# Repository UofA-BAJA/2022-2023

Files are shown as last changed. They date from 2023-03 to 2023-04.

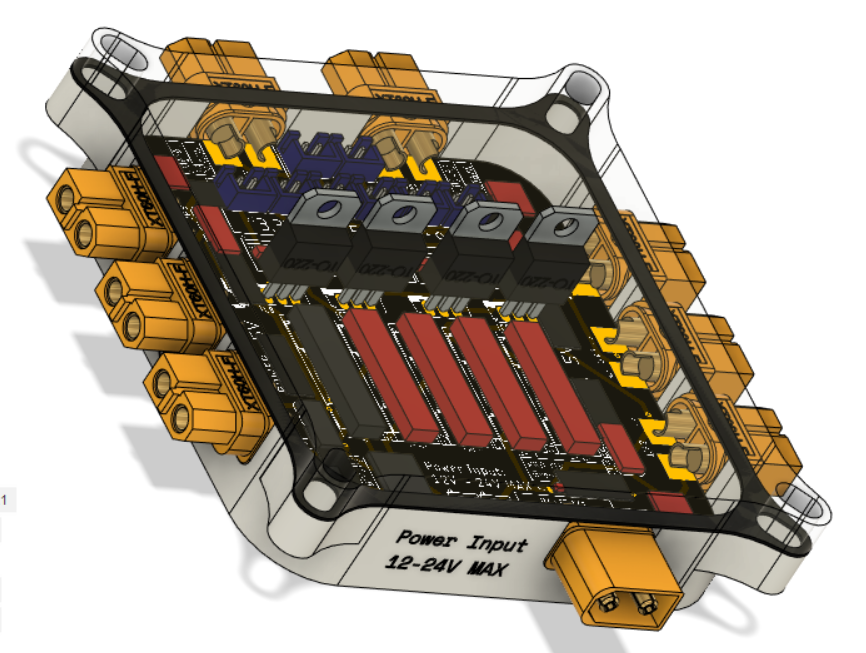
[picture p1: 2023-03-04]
res/Eagle Boards/Battery Board V1/Photos/battery_board_assembly_angle.png

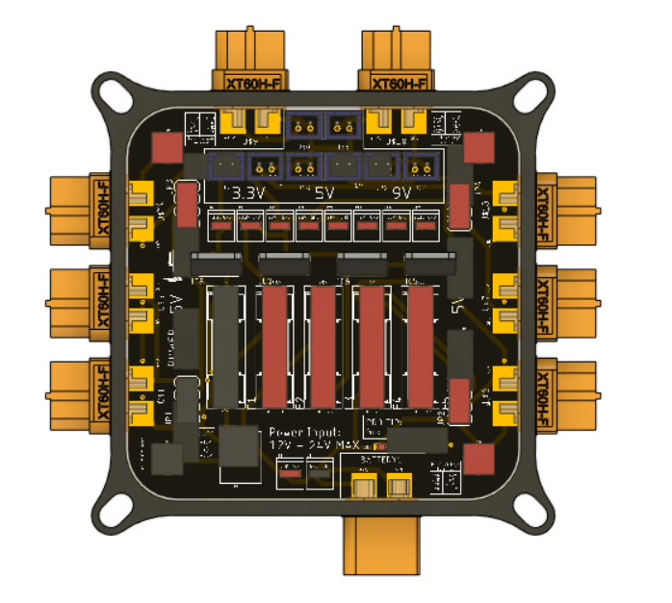
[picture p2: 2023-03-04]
res/Eagle Boards/Battery Board V1/Photos/battery_board_assembly_top.png

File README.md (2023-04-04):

# Electrical Team 2022-2023
This is the codebase for the University of Arizona BAJA Electrical Team, year 2022/2023.

[Google Drive Link](https://drive.google.com/drive/folders/1pqr16L63S9_5N_NZjZeFR-gvrg_NTns5?usp=sharing)

**This years officers and members include:**
Alex Romero (Electrical Lead),
Michael Byerly (Father),
Oliver Sjostrom,
Alyssa Pomerleau,
Henry Overbeck,
Liam Neu,
Muthu Krishnappan,
Man Doan,
Aeden Grandinetti,
Dorian Shay,
Aliah Haigh,
Juliana Levy
...

**Languages include:**
Python (Ground Station Systems),
C++ (Telemetry System),

Pull Requests into the Main Branch can be approved by Alex or Michael.
We also have a Codigna review bot that will automatically grade our code and offer suggestions in order to improve performance or legibility.

If you have any questions regarding any pieces of software or their functionality, please reach out to the officers.

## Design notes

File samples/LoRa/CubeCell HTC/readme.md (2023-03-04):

the link to the github for the HTC boards is [here](https://github.com/HelTecAutomation/CubeCell-Arduino)

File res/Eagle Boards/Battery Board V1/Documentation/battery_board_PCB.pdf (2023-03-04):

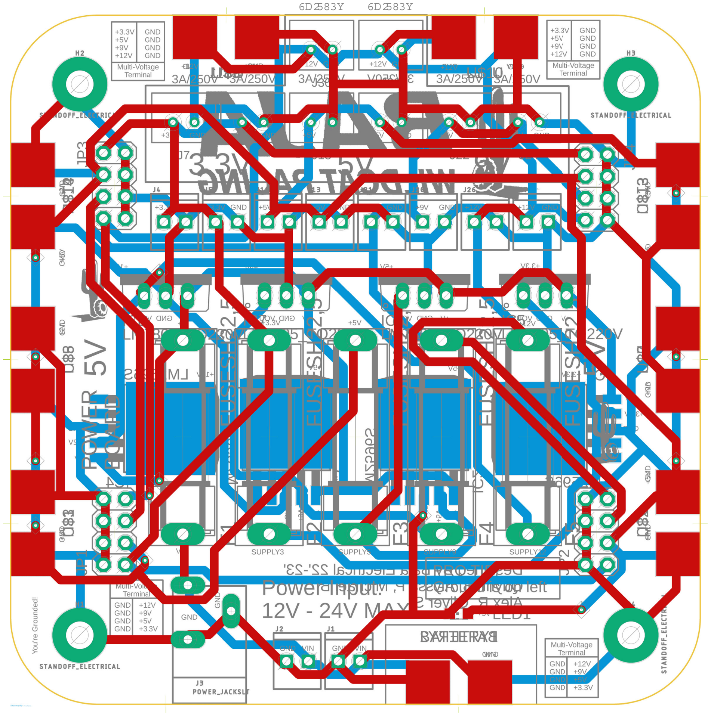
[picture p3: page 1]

3A/250V 3A/250V

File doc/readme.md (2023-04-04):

this folder is for documenation

To Get Setup
1. Install [Python](https://www.python.org/downloads/) if not installed
2. Install [VSCode](https://code.visualstudio.com/) if not installed
3. Install [Git](https://git-scm.com/download/win) and [Github Desktop](https://desktop.github.com/)
4. Open Git Repository in VSCode from Github Desktop and sign into github on VSCode
5. In terminal, execute the command "pip install PyQt5"
6. In terminal, execute the command "pip install pyqtgraph"
7. Go to src/Sensor Dashboard/\_\_main\_\_.py and hit run on VSCode

You are all setup!

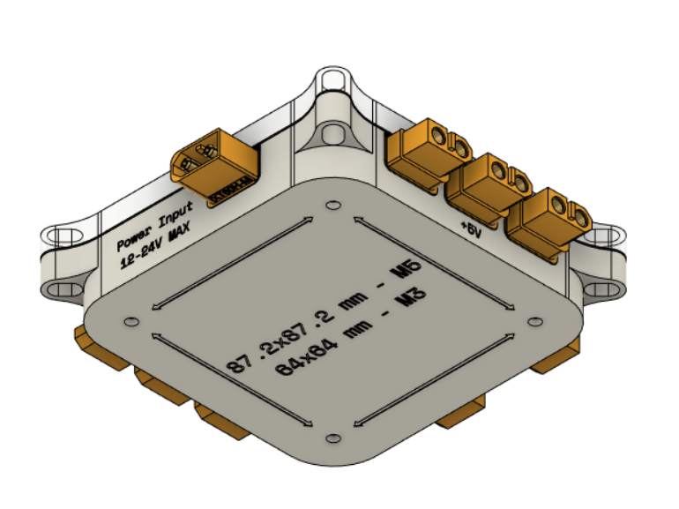
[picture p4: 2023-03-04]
res/Eagle Boards/Battery Board V1/Photos/Screenshot 2022-10-07 212603.png

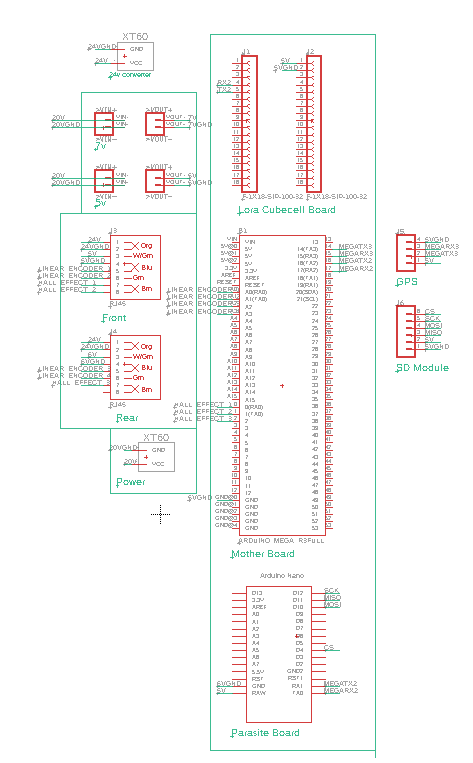
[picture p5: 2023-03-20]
res/Eagle Boards/image.png

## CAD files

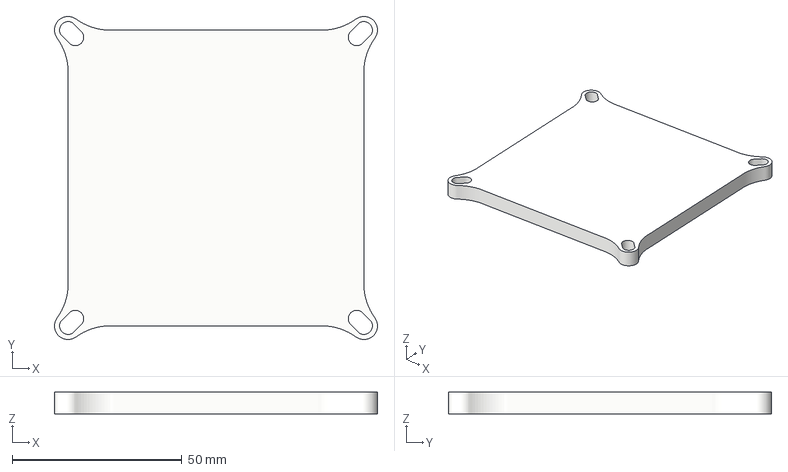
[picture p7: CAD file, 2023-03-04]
res/Eagle Boards/Battery Board V1/3D Files/Battery_Board_Lid.3mf
95.2 x 95.2 x 6.35 mm

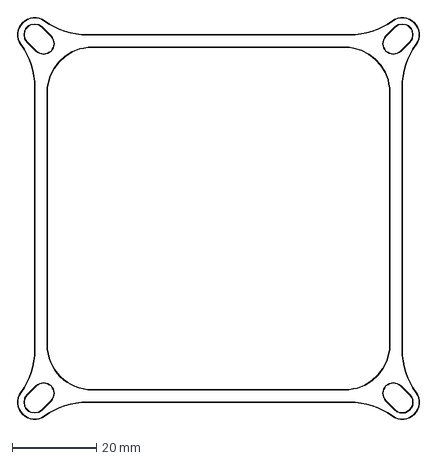
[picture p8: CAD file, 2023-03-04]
res/Eagle Boards/Battery Board V1/3D Files/Laser Cutter Files/battery_board_lid.dxf
96.0 x 96.0 mm

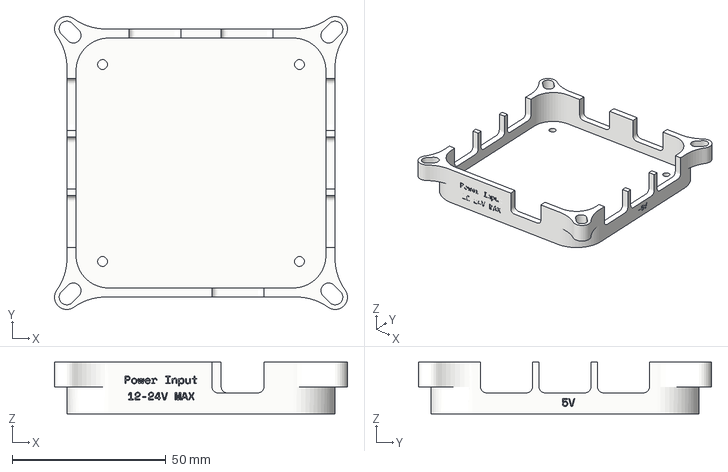
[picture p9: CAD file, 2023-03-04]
res/Eagle Boards/Battery Board V1/3D Files/Battery_Board_Case.3mf
95.2 x 95.2 x 16.8 mm

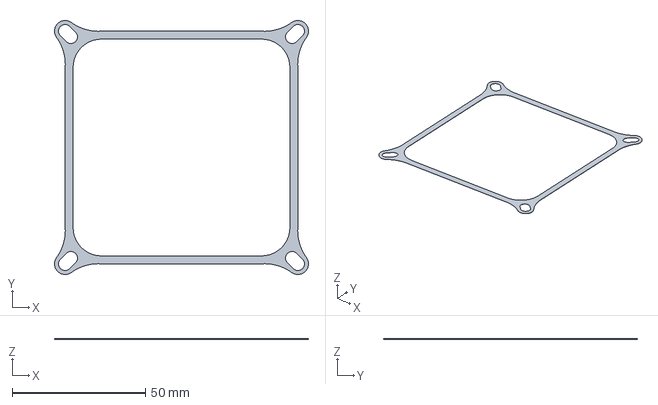
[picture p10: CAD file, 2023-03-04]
res/Eagle Boards/Battery Board V1/3D Files/Battery_Board_Seal.3mf
95.2 x 95.2 x 0.5 mm

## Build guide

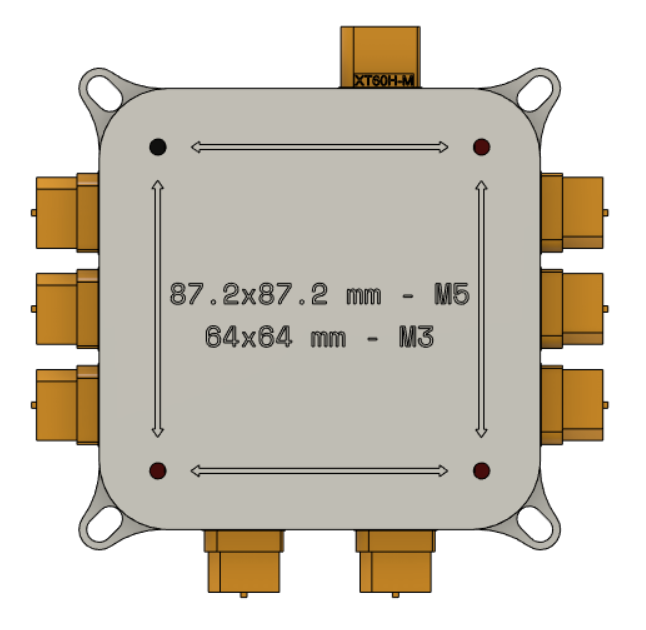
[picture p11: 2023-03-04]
res/Eagle Boards/Battery Board V1/Photos/battery_board_assembly_bottom.png

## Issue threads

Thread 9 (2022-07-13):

Issue Title: Update Straing Code

queball1999, 2022-07-13:
<!-- Edit the body of your new issue then click the ✓ "Create Issue" button in the top right of the editor. The first line will be the issue title. Assignees and Labels follow after a blank line. Leave an empty line before beginning the body of the issue. -->

Closed 2023-02-10.

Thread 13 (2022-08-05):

Test GPS examples on new board

queball1999, 2022-08-05:
Adding the board into the Arduino IDE and testing some of the examples. I uploaded some of the examples to the 2022-2023 repo.

Once everything was installed properly, this process went pretty smoothly. The GPS took a while to initialize, but that is to be expected. In the code, I'd like to change some things. I will create issues that we can work on later.

queball1999, 2022-08-05:
- Create UofA image on startup
- Delete HDOP
- Add number of sattelites
- Add units to altitude
- Convert speed to MPH
- Test with GPS antenna used last time

queball1999, 2022-08-06:
Actually decided against UofA image on startup. It would take up too much resources. Created progress bar instead for initialization.

Closed 2022-08-06.

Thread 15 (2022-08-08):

Configure LoRa GPS board to act as slave and send data to Raspberry Pi when requested

queball1999, 2022-08-08:
I want to be able to ask the GPS module for data using the Raspberry Pi. That way we can parse this data on the Pi and pack it in with the rest of the data, which will be transmitted to the ground station.

We first want to configure the LoRa GPS board with a method of transmission, TX/RX, or I2C. Once we decide this, we want to make the LoRa GPS board send data when requested from the Raspberry Pi. We probably want to pack the data and send it from the LoRa GPS board, then depack it and parse it on the Raspberry Pi.

queball1999, 2022-08-08:
### Cannot get the code to compile on CubeCell board:
*This happens on both Mac and PC

I have implemented I2C protocols in the code, but whenever I make 'Wire.onRequest()' or 'Wire.onReceive()' calls the code will not compile; it keeps giving me the following error:

`undefined reference to TwoWire::onReceive(void (*)(int))`
`collect2.exe: error: ld returned 1 exit status`
`exit status 1`
`Error compiling for board CubeCell-GPS（HTCC-AB02S）.`

The following code is what I am currently using:
`#define MASTER_ADDRESS 0x04`
...
`void setup() {`
   `Wire.begin(MASTER_ADDRESS);`
   `Wire.onReceive(receiveEvent);`
   `Wire.onRequest(requestEvent);`
`}`
...
`void receiveEvent(int bytes) {`
`Wire.read();`
`}`

`void requestEvent() {`
`Wire.write('test')`
`}`

I am wondering if something is wrong with the code or if something is wrong with the board inside of the Arduino IDE. I did find a forum that talked about this issue and had possible solutions for Mac and Windows, but I was unsuccessful in getting it to work. The issue only happens when the calls to 'Wire.onRequest()' or 'Wire.onReceive()' are made.

queball1999, 2022-08-11:
After talking with Michael and doing a bit of research into the board, we may just implement Serial communication protocols instead of I2C. It seems like the OLED screen is using I2C, so the board has I2C, I just don't know why its not working.

Closed 2023-02-10.

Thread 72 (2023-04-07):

Variables overflowing when byte map is incomplete

B-i-x, 2023-04-07:
<!-- Edit the body of your new issue then click the ✓ "Create Issue" button in the top right of the editor. The first line will be the issue title. Assignees and Labels follow after a blank line. Leave an empty line before beginning the body of the issue. -->

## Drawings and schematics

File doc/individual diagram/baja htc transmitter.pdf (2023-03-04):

## In HTC, BUSY is digital

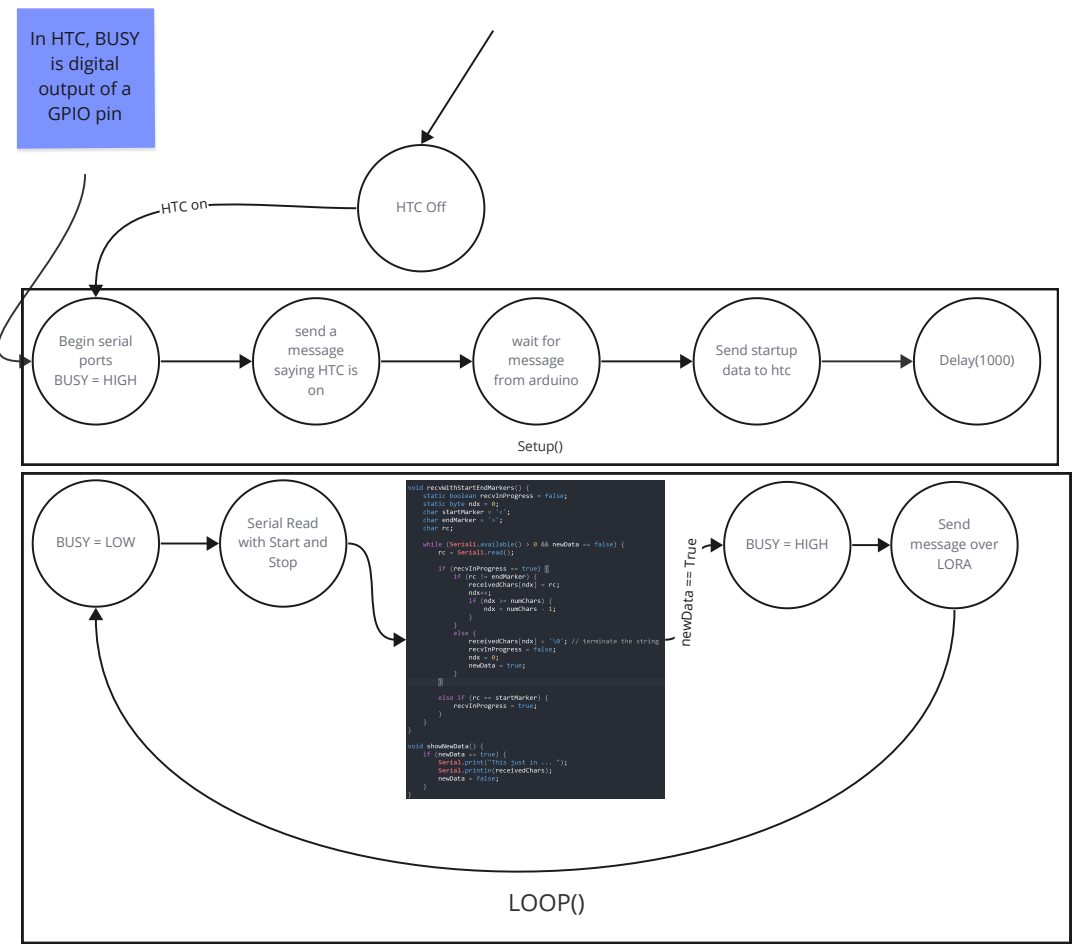
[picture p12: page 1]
HTC Off; Begin serial ports BUSY = HIGH; wait for message from arduino; HTC on; Delay(1000); output of a GPIO pin; Setup(); BUSY = LOW; BUSY = HIGH; newData == True; Send message over LORA; LOOP()

send a
message
saying HTC is

Send startup
data to htc

Serial Read
with Start and
Stop

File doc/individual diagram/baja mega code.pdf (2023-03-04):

## Global Variables

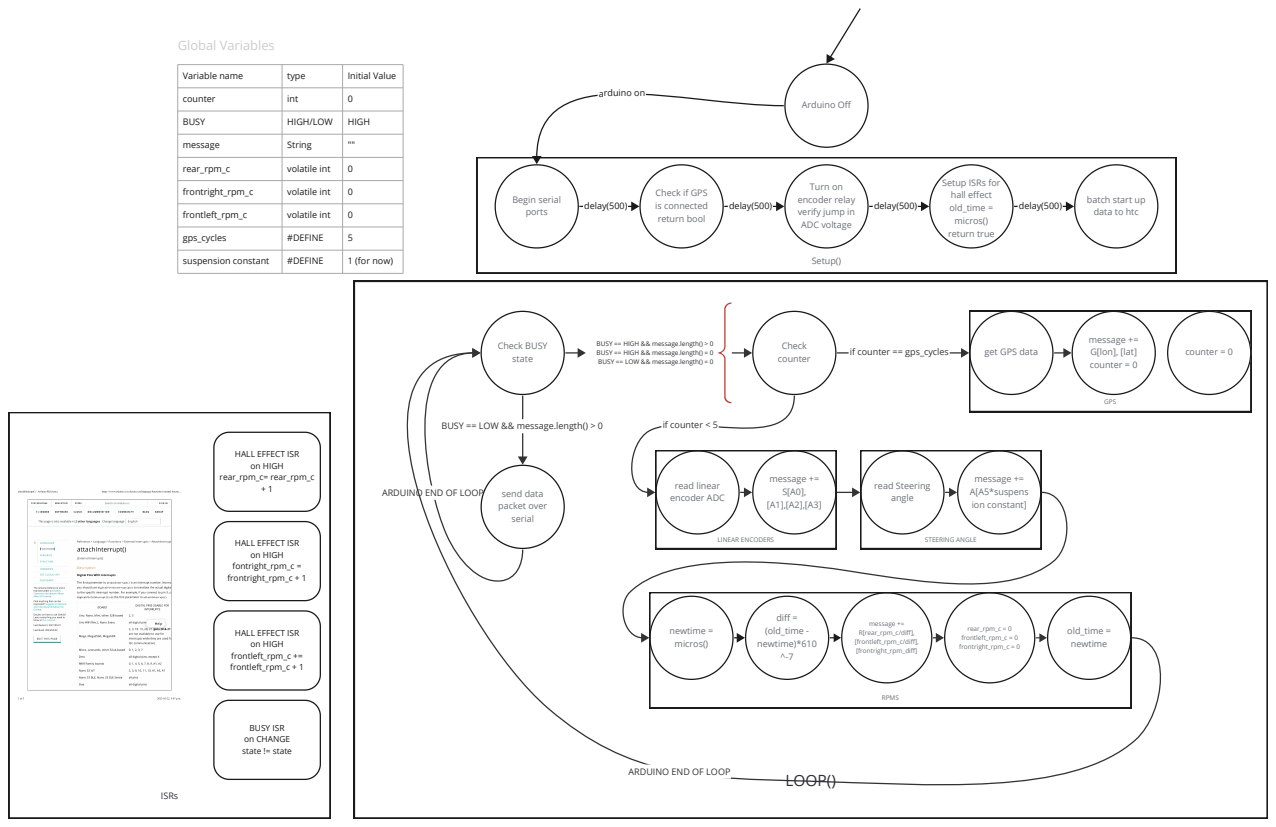
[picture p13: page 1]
Arduino Off; Begin serial ports; arduino on; delay(500); Setup(); Check BUSY state; send data packet over serial; read linear encoder ADC; newtime = micros(); diff = (old_time - newtime)*610 ^-7; message += R[rear_rpm_c/diff], [frontleft_rpm_c/diff], [frontright_rpm_diff]; HALL EFFECT ISR on HIGH fontright_rpm_c = frontright_rpm_c + 1; HALL EFFECT ISR on HIGH frontleft_rpm_c += frontleft_rpm_c + 1; BUSY ISR on CHANGE state != state; Check counter; volatile int; rear_rpm_c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

Variable name | type | Initial Value

counter | int | 0

BUSY | HIGH/LOW | HIGH

message | String | ""

Setup ISRs for
hall effect
old_time =
micros()
return true

frontright_rpm_c | volatile int | 0

Turn on
encoder relay
verify jump in
ADC voltage

Check if GPS
is connected
return bool

batch start up
data to htc

frontleft_rpm_c | volatile int | 0

gps_cycles | #DEFINE | 5

suspension constant | #DEFINE | 1 (for now)

BUSY == HIGH && message.length() > 0
BUSY == HIGH && message.length() = 0
BUSY == LOW && message.length() = 0

get GPS data

BUSY == LOW && message.length() > 0

HALL EFFECT ISR
on HIGH
rear_rpm_c= rear_rpm_c

ARDUINO END OF LOOP

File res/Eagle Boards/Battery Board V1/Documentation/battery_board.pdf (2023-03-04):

## 3A/250V 3A/250V

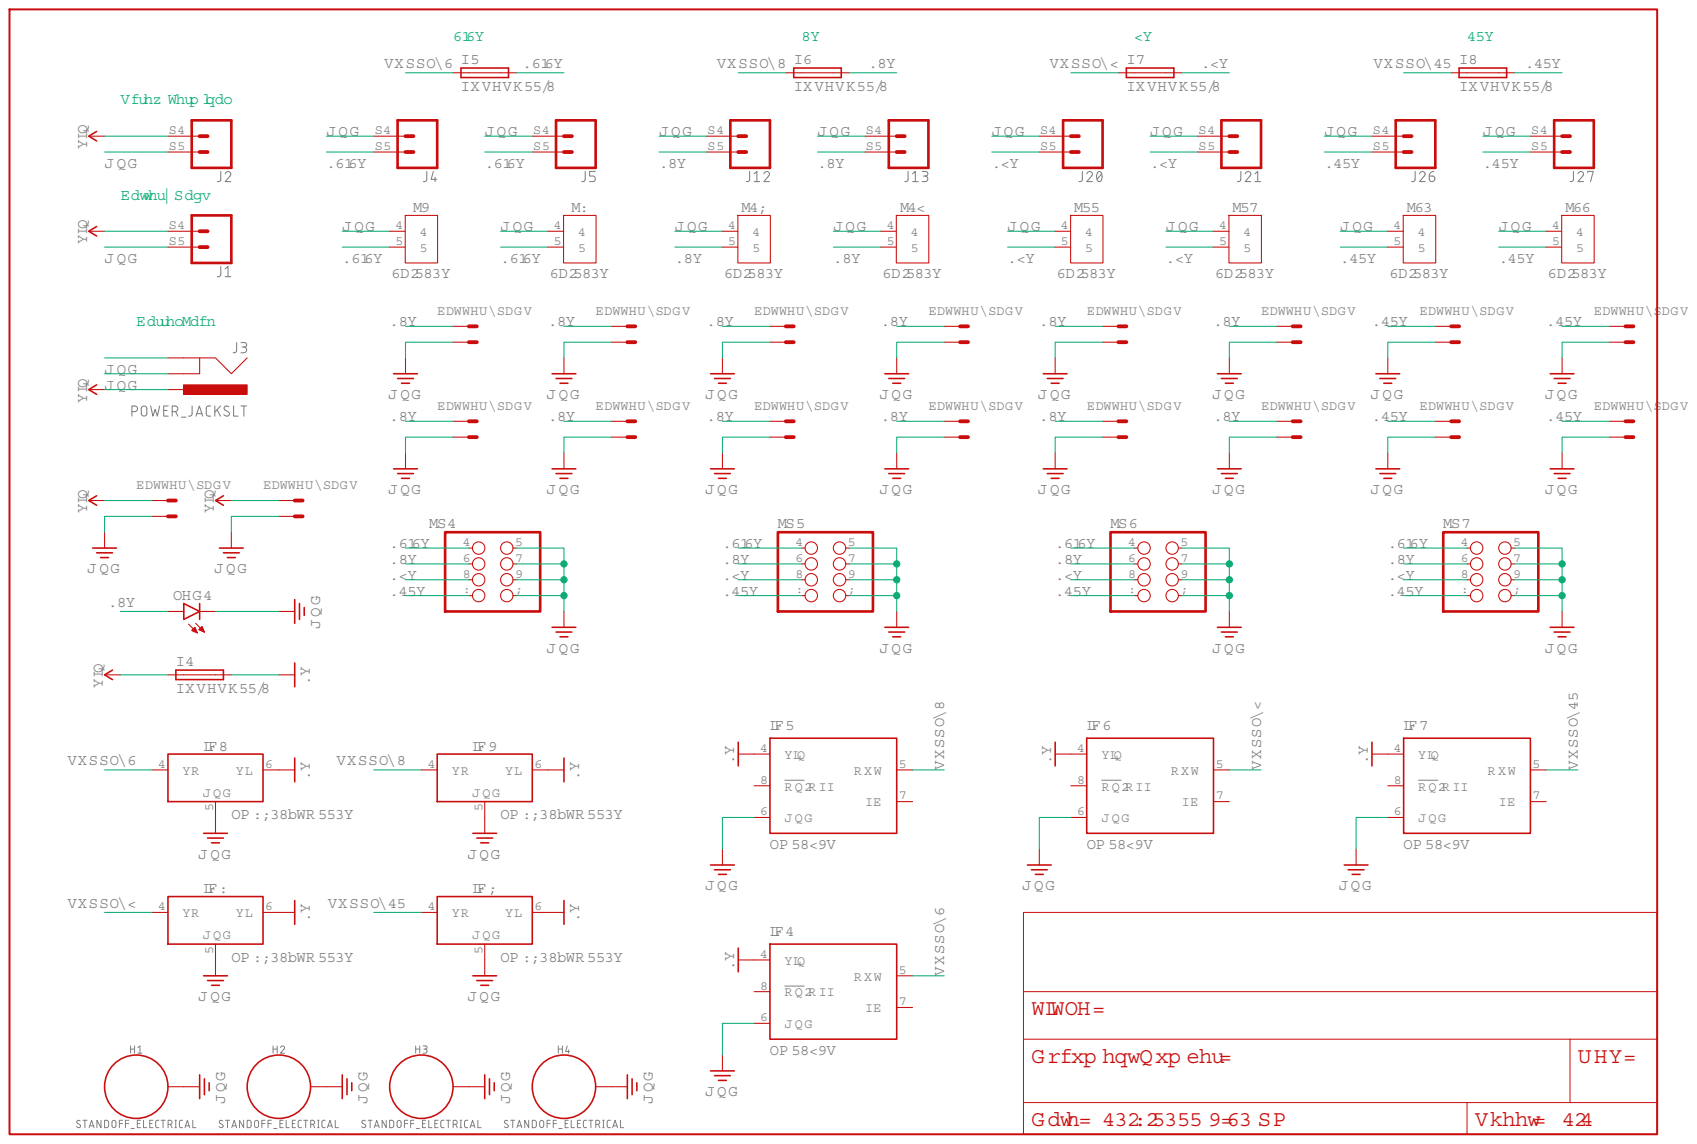
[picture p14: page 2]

D ocum entN um ber:

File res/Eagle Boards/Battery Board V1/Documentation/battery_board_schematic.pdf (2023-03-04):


D ocum entN um ber:

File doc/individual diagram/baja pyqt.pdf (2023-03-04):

## idk what to put

here honestly,

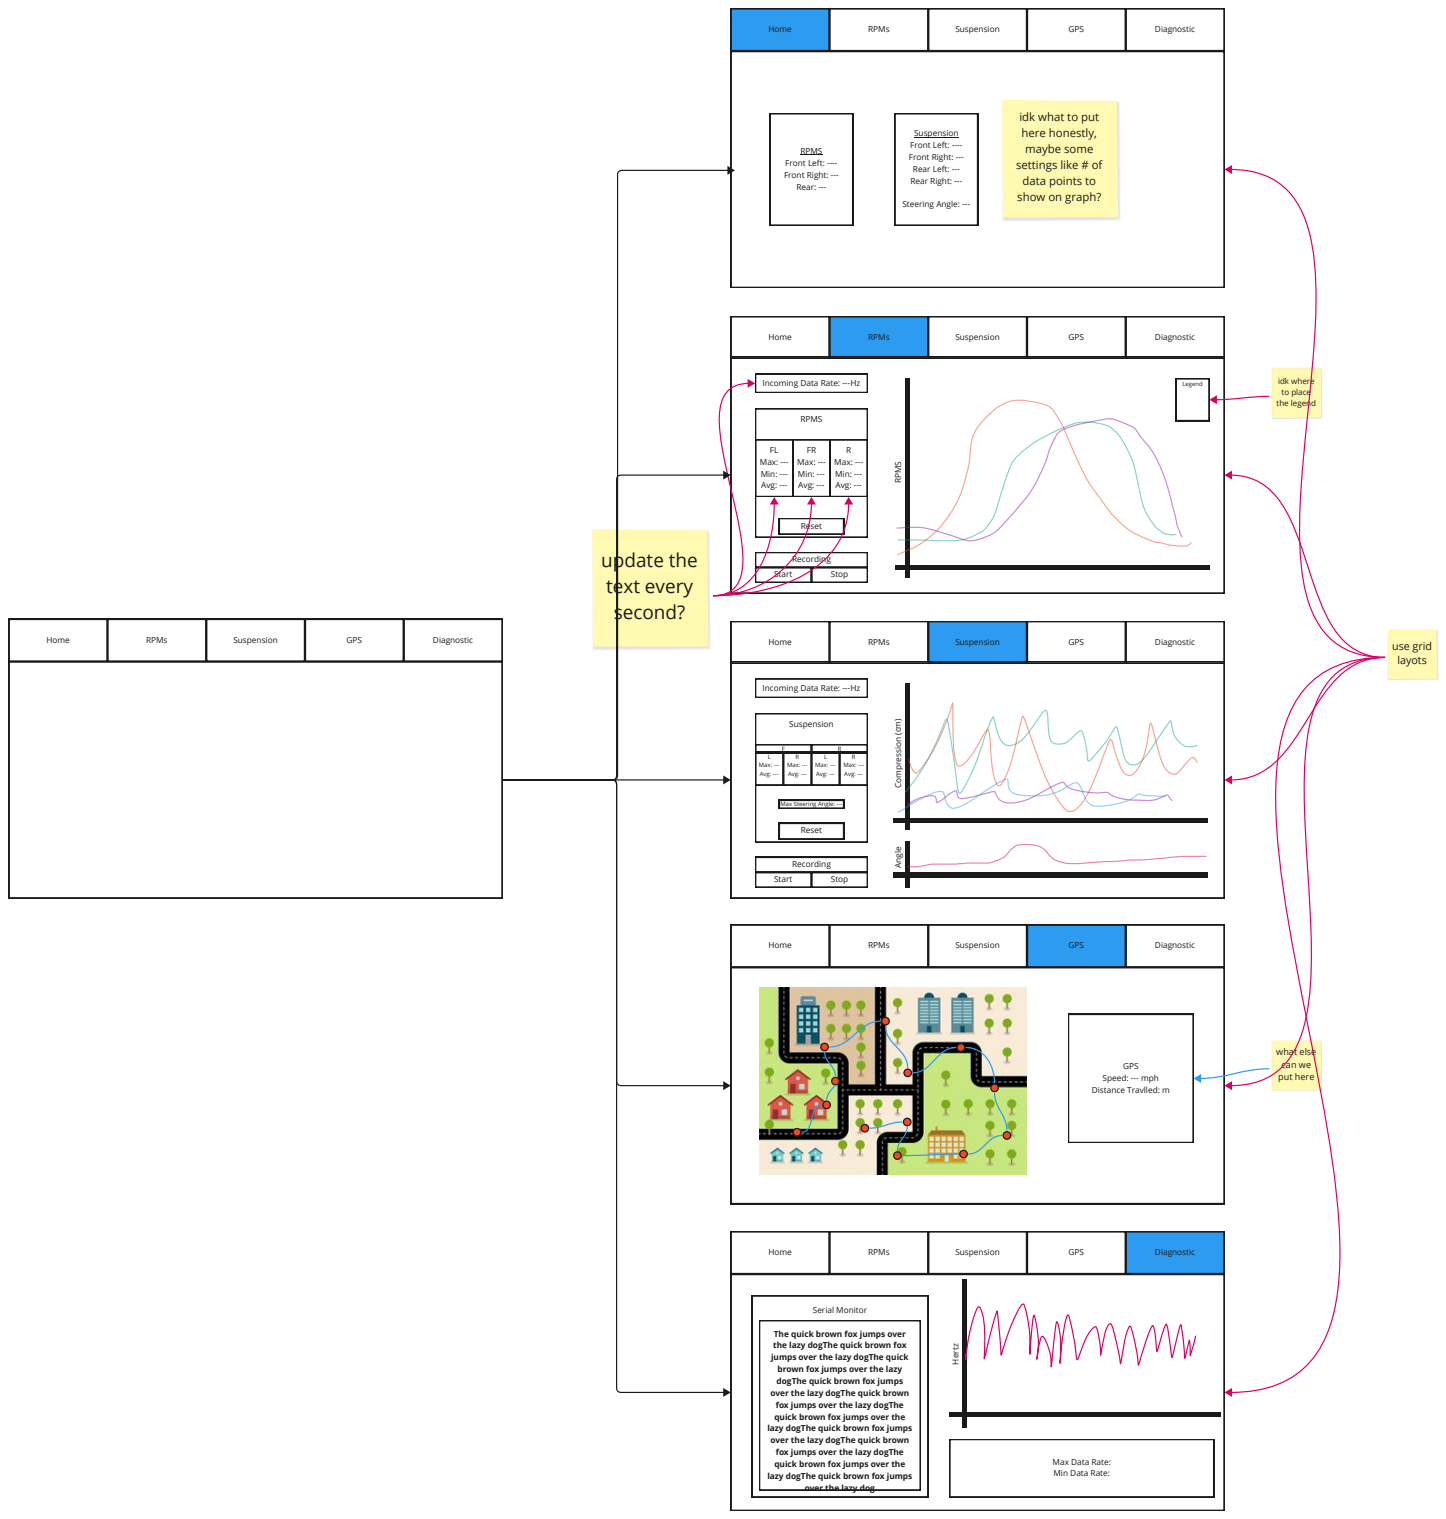
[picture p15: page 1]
Home; RPMs; Suspension; GPS; Diagnostic; RPMS Front Left: ---- Front Right: --- Rear: ---; Suspension Front Left: ---- Front Right: --- Rear Left: --- Rear Right: ---; Steering Angle: ---; RPMS; Reset; Start; Stop; Recording; Avg: ---; R Max: --- Min: ---; update the text every second?; Compression (cm); Angle; Legend; idk where to place; the legend; Hertz; Serial Monitor; use grid layots

maybe some
settings like # of
data points to
show on graph?

Incoming Data Rate: ---Hz

FL Max: --- Min: ---

FR Max: --- Min: ---

L Max: ---Avg: --- | R Max: ---Avg: --- | L Max: ---Avg: --- | R Max: ---Avg: ---

Max Steering Angle: ---

what else
can we put here

GPS
Speed: --- mph Distance Travlled: m

The quick brown fox jumps over
the lazy dogThe quick brown fox
jumps over the lazy dogThe quick
brown fox jumps over the lazy
dogThe quick brown fox jumps
over the lazy dogThe quick brown
fox jumps over the lazy dogThe
quick brown fox jumps over the
lazy dogThe quick brown fox jumps

Max Data Rate: Min Data Rate:

over the lazy dog

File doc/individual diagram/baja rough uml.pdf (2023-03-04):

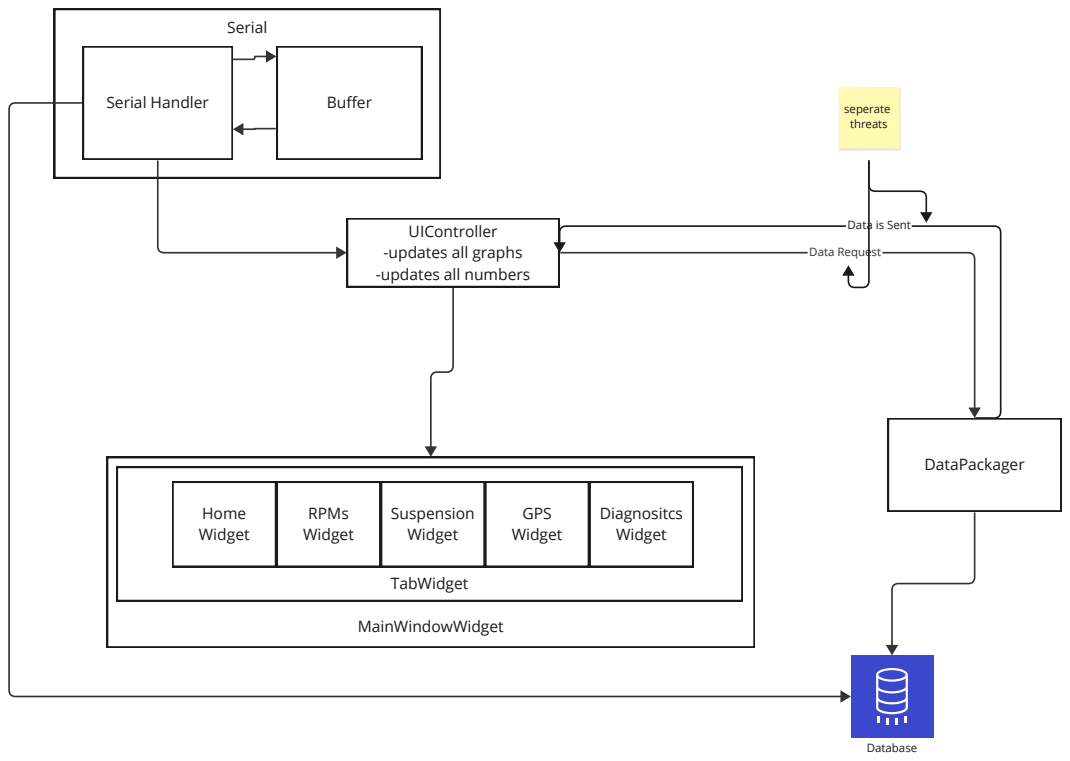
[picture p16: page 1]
TabWidget; Home Widget; RPMs Widget; Suspension Widget; GPS Widget; Diagnositcs Widget; MainWindowWidget; Serial; DataPackager; Database; seperate threats; Serial Handler; Buffer

Data is Sent
Data Request

UIController
-updates all graphs
-updates all numbers

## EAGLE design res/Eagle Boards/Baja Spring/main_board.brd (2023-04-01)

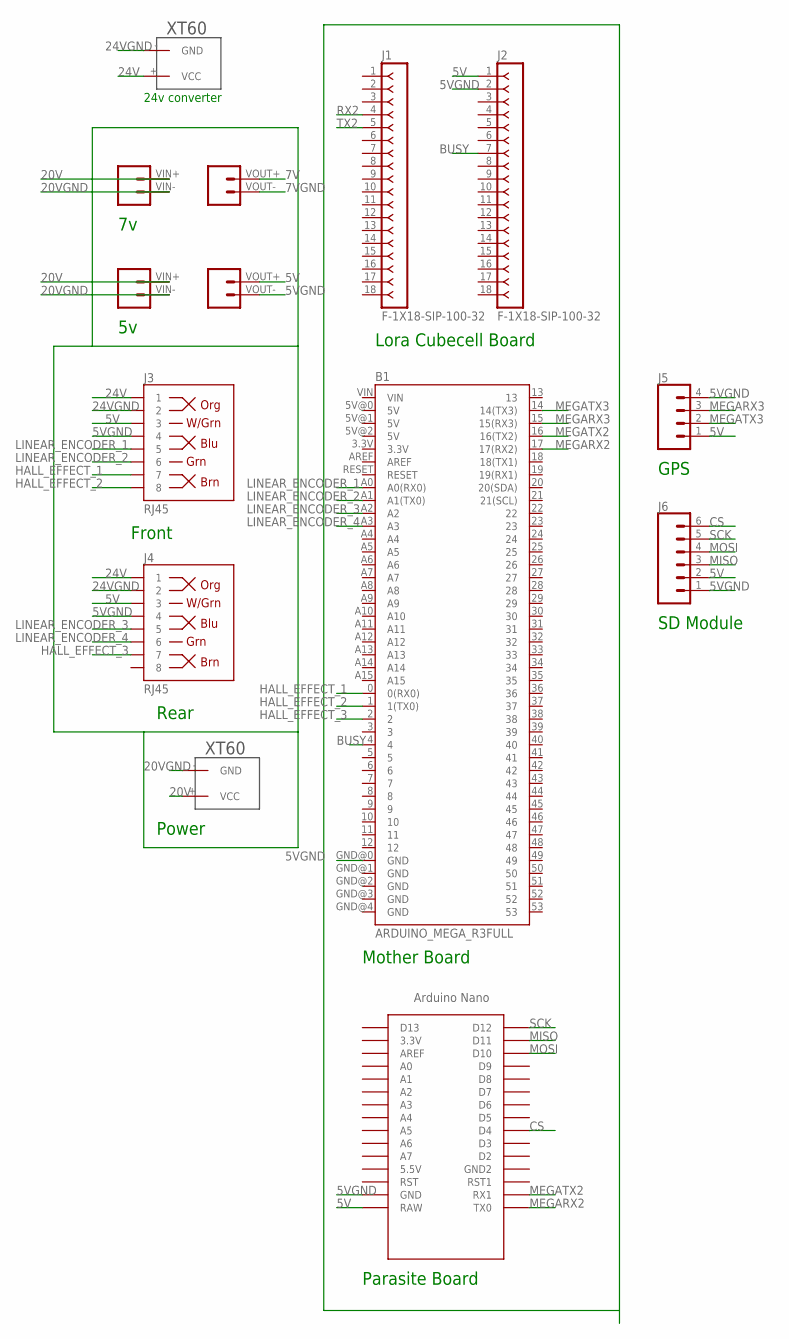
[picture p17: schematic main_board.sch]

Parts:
B1: ARDUINO_MEGA_R3FULL; ARDUINO_MEGA
J1, J2: F-1X18-SIP-100-32; SIP-100-18-32
J3, J4: RJ45; RJ45-8
J5: CONN_04; 1X04
J6: CONN_06NO_SILK_NO_POP; 1X06_NO_SILK
U$1: NANO
U$2, U$5: XT60
U$3, U$4: BUCKPINSBUCK; 1X03_LONGPADS

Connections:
5V: J2.1, J3.3, J4.3, J5.1, J6.2, U$1.RAW, U$4.VOUT+ (4)
5VGND: B1.GND@0 (GND), J2.2, J3.4, J4.4, J5.4, J6.1, U$1.GND, U$4.VOUT- (3)
7V: U$3.VOUT+ (4)
7VGND: U$3.VOUT- (3)
20V: U$2.+ (VCC), U$3.VIN+ (2), U$4.VIN+ (2)
20VGND: U$2.- (GND), U$3.VIN- (1), U$4.VIN- (1)
24V: J3.1, J4.1, U$5.+ (VCC)
24VGND: J3.2, J4.2, U$5.- (GND)
BUSY: B1.4, J2.7
CS: J6.6, U$1.D4
HALL_EFFECT_1: B1.0 (0(RX0)), J3.7
HALL_EFFECT_2: B1.1 (1(TX0)), J3.8
HALL_EFFECT_3: B1.2, J4.7
LINEAR_ENCODER_1: B1.A0 (A0(RX0)), J3.5
LINEAR_ENCODER_2: B1.A1 (A1(TX0)), J3.6
LINEAR_ENCODER_3: B1.A2, J4.5
LINEAR_ENCODER_4: B1.A3, J4.6
MEGARX2: B1.17 (17(RX2)), U$1.TX0
MEGARX3: B1.15 (15(RX3)), J5.3
MEGATX2: B1.16 (16(TX2)), U$1.RX1
MEGATX3: B1.14 (14(TX3)), J5.2
MISO: J6.3, U$1.D11
MOSI: J6.4, U$1.D10
RX2: J1.4
SCK: J6.5, U$1.D12
TX2: J1.5

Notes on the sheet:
Parasite Board
Lora Cubecell Board
Mother Board
Front
Rear
Power
GPS
SD Module
24v converter

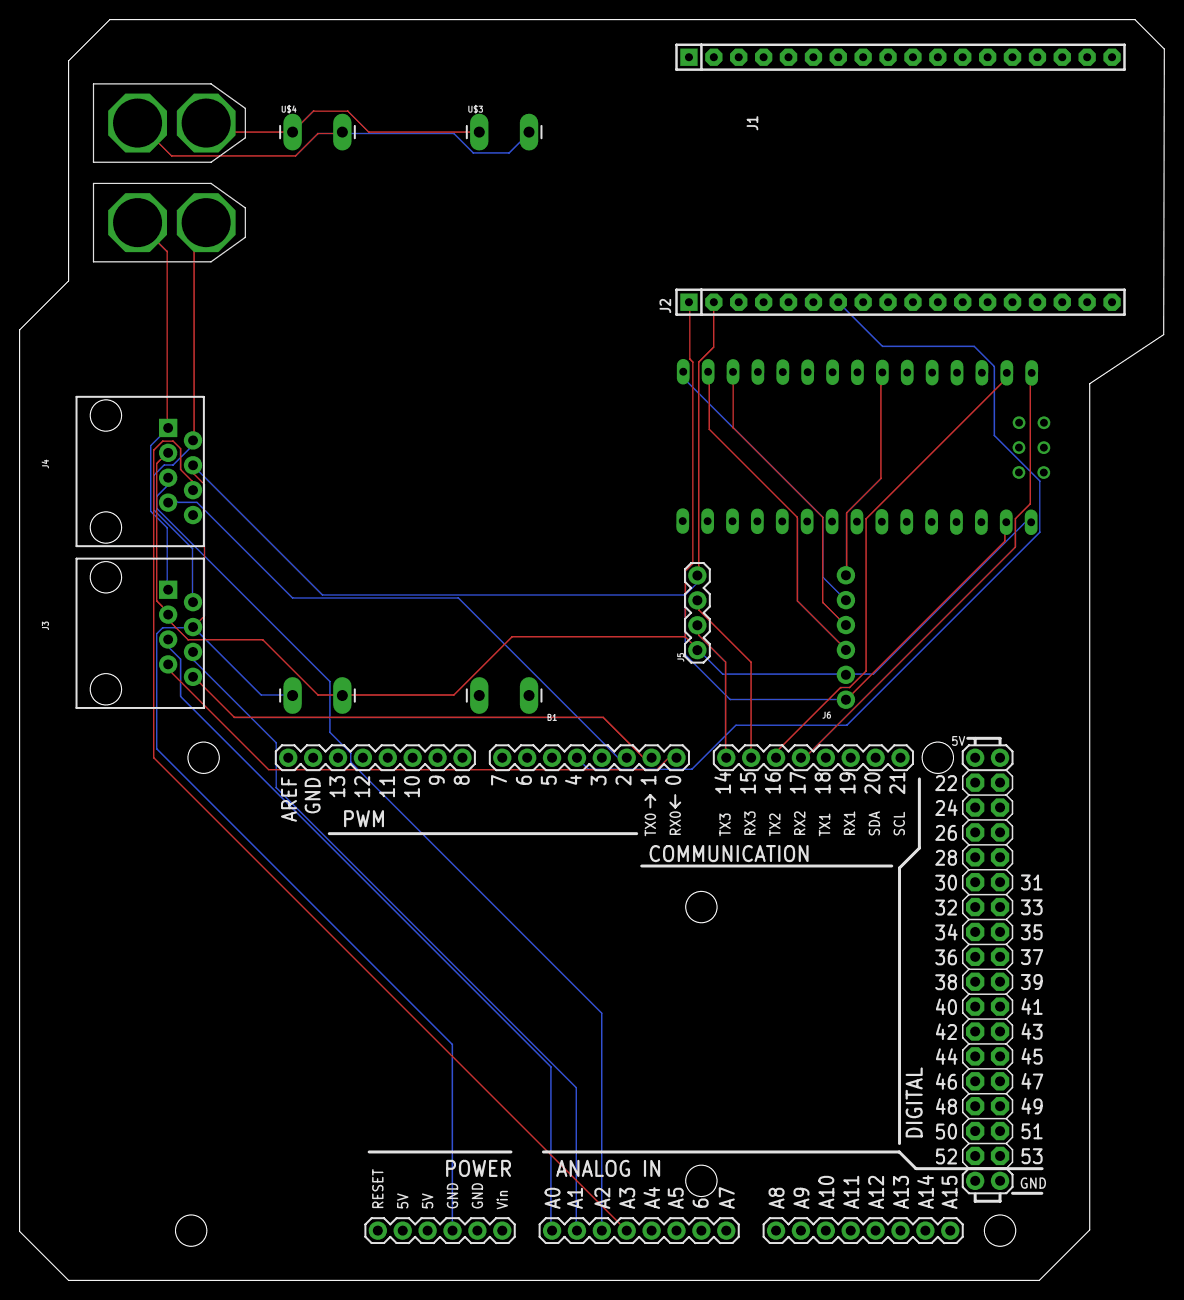
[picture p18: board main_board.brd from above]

Board: 2 copper layers, 116.8 x 128.7 mm, 12 parts (0 on the bottom side), 22 nets.

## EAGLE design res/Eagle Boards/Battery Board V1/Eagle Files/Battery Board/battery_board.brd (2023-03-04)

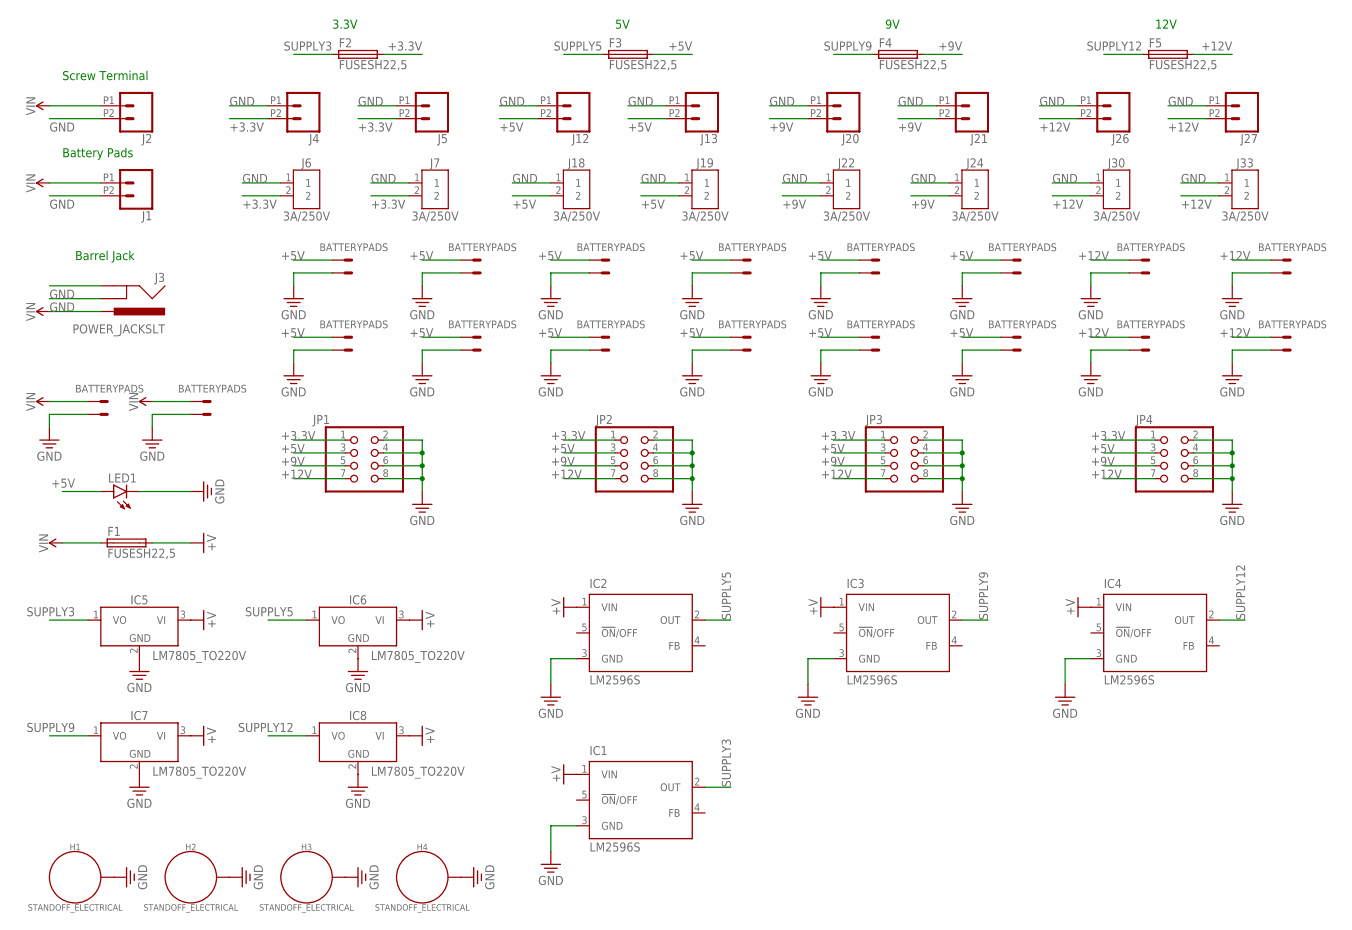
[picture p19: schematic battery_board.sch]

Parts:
BATTERY1, BATTERY2: BATTERYPADS; DIODFN1228X508X30-2N
F1, F2, F3, F4, F5: FUSESH22,5; SH22,5
H1, H2, H3, H4: STANDOFF_ELECTRICAL; STANDOFF-ELECTRICAL
IC1, IC2, IC3, IC4: LM2596S; TO263-5
IC5, IC6, IC7, IC8: LM7805_TO220V; TO220V
J1, J2, J4, J5, J12, J13, J20, J21, J26, J27: CONN_022.54MM_SCREWTERM; 1X02_2.54_SCREWTERM
J3: POWER_JACKSLT; POWER_JACK_SLOT
J6, J7, J18, J19, J22, J24, J30, J33: 3A/250V; B2B-XH-A
JP1, JP2, JP3, JP4: PINHD-2X4; 2X04
LED1: LEDCHIP-LED0805; CHIP-LED0805
U$1, U$2, U$3, U$4, U$5, U$6, U$7, U$8, U$9, U$10, U$11, U$12, U$13, U$14, U$15, U$16: BATTERYPADS; DIODFN1228X508X30-2N

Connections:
+3.3V: F2.2, J4.P2 (2), J5.P2 (2), J6.2, J7.2, JP1.1, JP2.1, JP3.1, JP4.1
+5V: F3.2, J12.P2 (2), J13.P2 (2), J18.2, J19.2, JP1.3, JP2.3, JP3.3, JP4.3, LED1.A, U$1.VIN, U$2.VIN, U$3.VIN, U$4.VIN, U$5.VIN, U$6.VIN, U$7.VIN, U$8.VIN, U$13.VIN, U$14.VIN, U$15.VIN, U$16.VIN
+9V: F4.2, J20.P2 (2), J21.P2 (2), J22.2, J24.2, JP1.5, JP2.5, JP3.5, JP4.5
+12V: F5.2, J26.P2 (2), J27.P2 (2), J30.2, J33.2, JP1.7, JP2.7, JP3.7, JP4.7, U$9.VIN, U$10.VIN, U$11.VIN, U$12.VIN
+V: F1.2, IC1.1 (VIN), IC2.1 (VIN), IC3.1 (VIN), IC4.1 (VIN), IC5.3 (VI), IC6.3 (VI), IC7.3 (VI), IC8.3 (VI)
GND: BATTERY1.GND, BATTERY2.GND, H1.P1, H2.P1, H3.P1, H4.P1, IC1.3 (GND), IC2.3 (GND), IC3.3 (GND), IC4.3 (GND), IC5.2 (GND), IC6.2 (GND), IC7.2 (GND), IC8.2 (GND), J1.P2 (2), J2.P2 (2), J3.GND@1 (GNDBREAK), J3.GND@2 (GND), J4.P1 (1), J5.P1 (1), J6.1, J7.1, J12.P1 (1), J13.P1 (1), J18.1, J19.1, J20.P1 (1), J21.P1 (1), J22.1, J24.1, J26.P1 (1), J27.P1 (1), J30.1, J33.1, JP1.2, JP1.4, JP1.6, JP1.8, JP2.2, JP2.4, JP2.6, JP2.8, JP3.2, JP3.4, JP3.6, JP3.8, JP4.2, JP4.4, JP4.6, JP4.8, LED1.C, U$1.GND, U$2.GND, U$3.GND, U$4.GND, U$5.GND, U$6.GND, U$7.GND, U$8.GND, U$9.GND, U$10.GND, U$11.GND, U$12.GND, U$13.GND, U$14.GND, U$15.GND, U$16.GND
SUPPLY3: F2.1, IC1.2 (OUT), IC5.1 (VO)
SUPPLY5: F3.1, IC2.2 (OUT), IC6.1 (VO)
SUPPLY9: F4.1, IC3.2 (OUT), IC7.1 (VO)
SUPPLY12: F5.1, IC4.2 (OUT), IC8.1 (VO)
VIN: BATTERY1.VIN, BATTERY2.VIN, F1.1, J1.P1 (1), J2.P1 (1), J3.PWR

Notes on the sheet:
Screw Terminal
Battery Pads
Barrel Jack
12V
3.3V

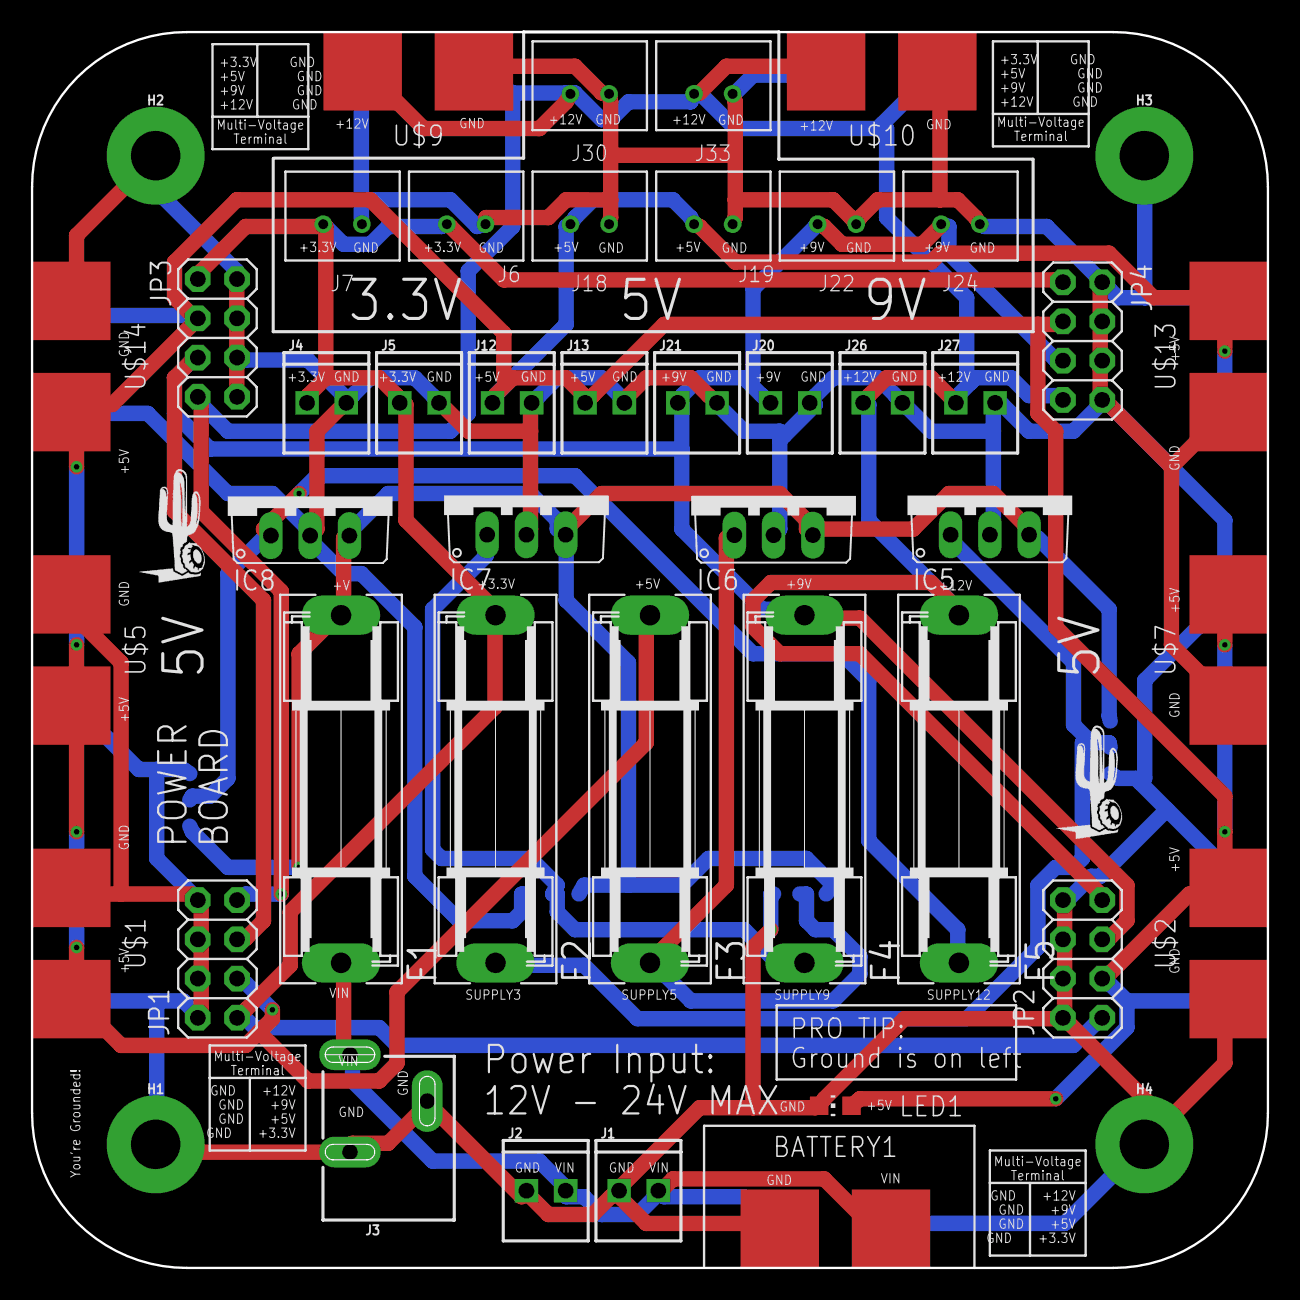
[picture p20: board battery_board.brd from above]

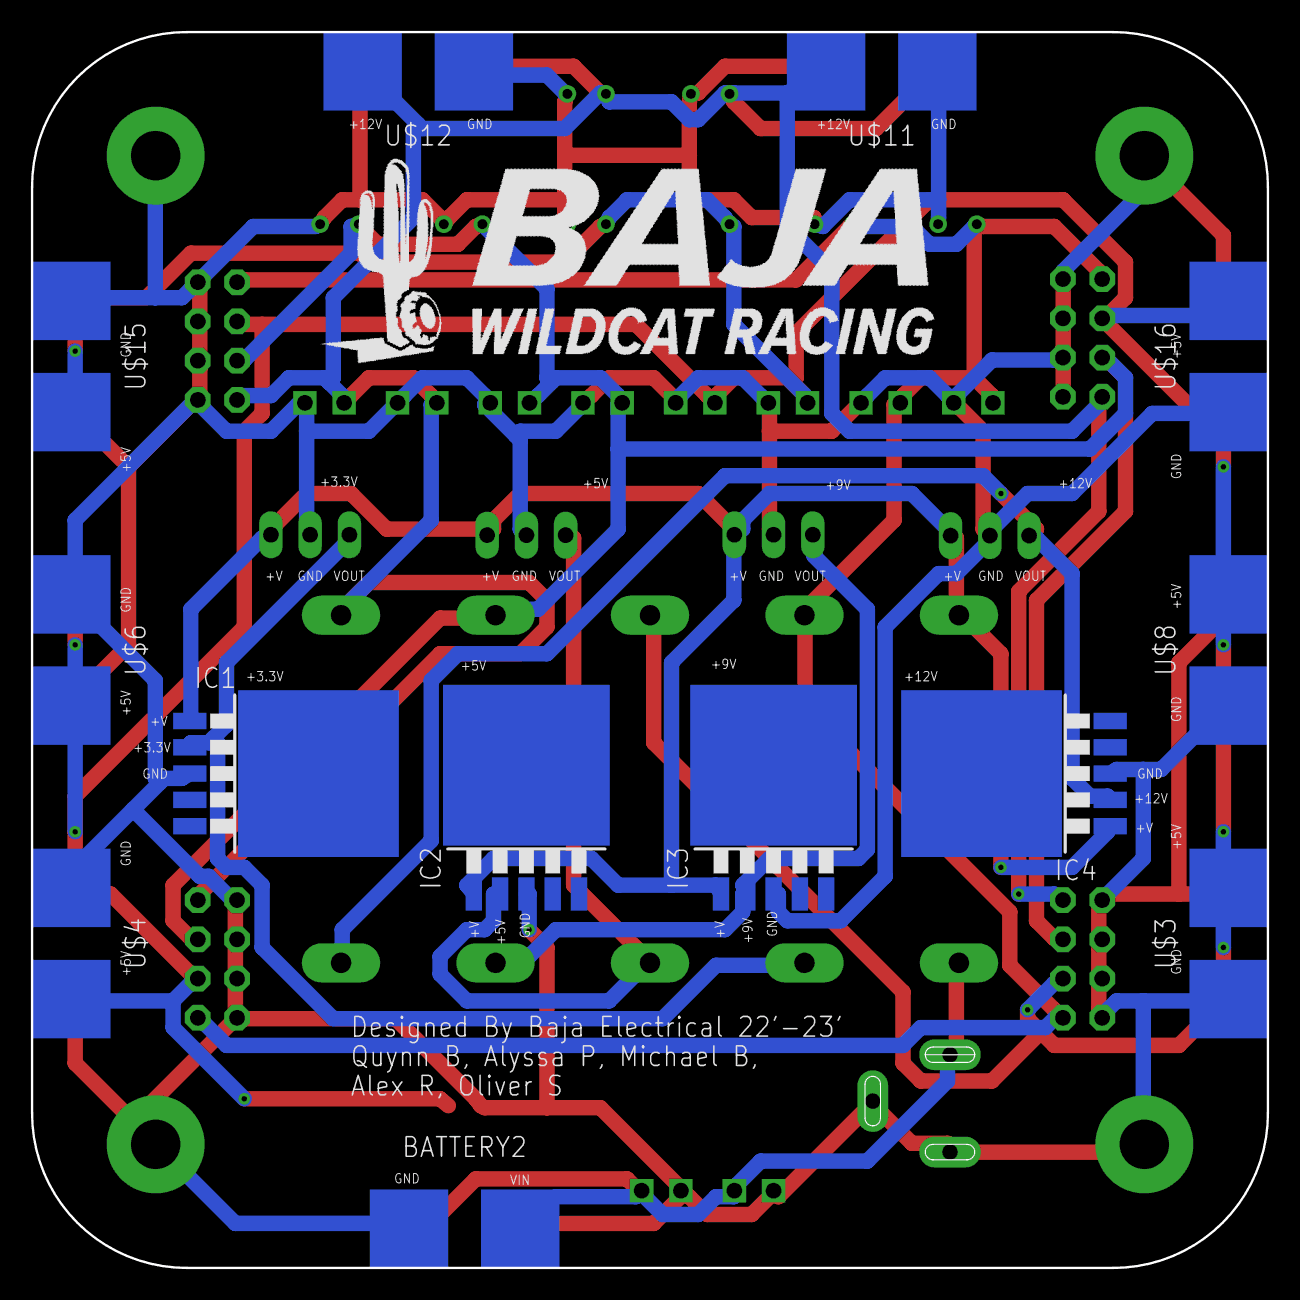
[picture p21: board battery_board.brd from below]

Board: 2 copper layers, 80.0 x 80.0 mm, 59 parts (13 on the bottom side), 11 nets.

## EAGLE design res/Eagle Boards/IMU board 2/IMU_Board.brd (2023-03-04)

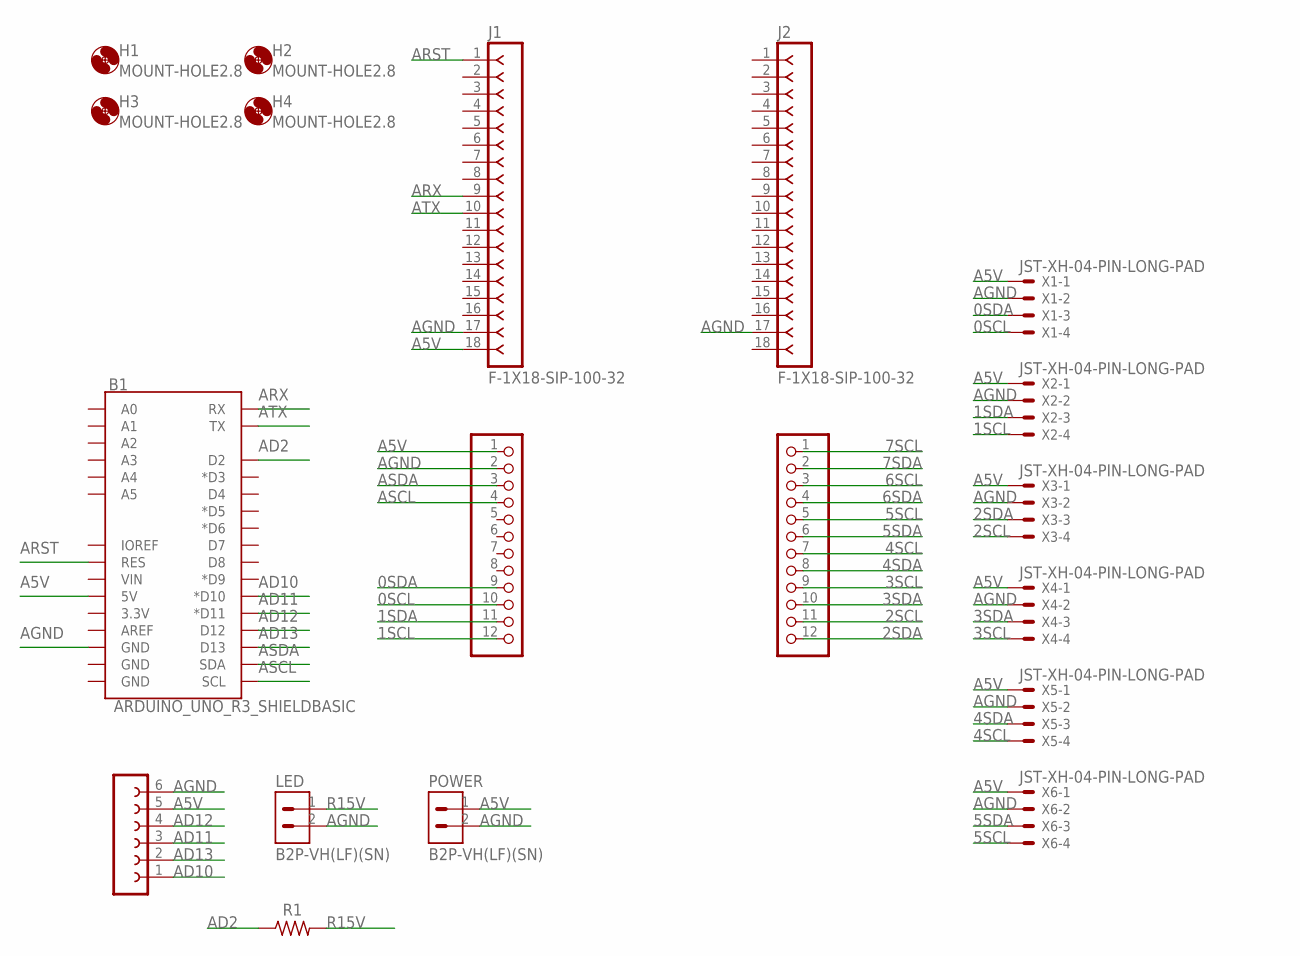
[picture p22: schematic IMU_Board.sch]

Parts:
B1: ARDUINO_UNO_R3_SHIELDBASIC; UNO_R3_SHIELD
H1, H2, H3, H4: MOUNT-HOLE2.8; 2,8
J1, J2: F-1X18-SIP-100-32; SIP-100-18-32
JP1, JP3: HEADER-1X12; 1X12_ROUND
LED: B2P-VH(LF)(SN); HDR-02
POWER: B2P-VH(LF)(SN); HDR-02
R1: R-US_AXIAL-11.7MM-PITCH; RESAD1176W63L850D250B
SD: FE06-1; FE06
X1, X2, X3, X4, X5, X6: JST-XH-04-PIN-LONG-PAD; JST-XH-04-PACKAGE-LONG-PAD

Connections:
0SCL: JP3.10, X1.4
0SDA: JP3.9, X1.3
1SCL: JP3.12, X2.4
1SDA: JP3.11, X2.3
2SCL: JP1.11, X3.4
2SDA: JP1.12, X3.3
3SCL: JP1.9, X4.4
3SDA: JP1.10, X4.3
4SCL: JP1.7, X5.4
4SDA: JP1.8, X5.3
5SCL: JP1.5, X6.4
5SDA: JP1.6, X6.3
6SCL: JP1.3
6SDA: JP1.4
7SCL: JP1.1
7SDA: JP1.2
A5V: B1.5V, J1.18, JP3.1, POWER.1, SD.5, X1.1, X2.1, X3.1, X4.1, X5.1, X6.1
AD2: B1.D2, R1.1
AD10: B1.D10 (*D10), SD.1
AD11: B1.D11 (*D11), SD.3
AD12: B1.D12, SD.4
AD13: B1.D13, SD.2
AGND: B1.GND@2 (GND), J1.17, J2.17, JP3.2, LED.2, POWER.2, SD.6, X1.2, X2.2, X3.2, X4.2, X5.2, X6.2
ARST: B1.RES, J1.1
ARX: B1.RX, J1.9
ASCL: B1.SCL, JP3.4
ASDA: B1.SDA, JP3.3
ATX: B1.TX, J1.10
R15V: LED.1, R1.2

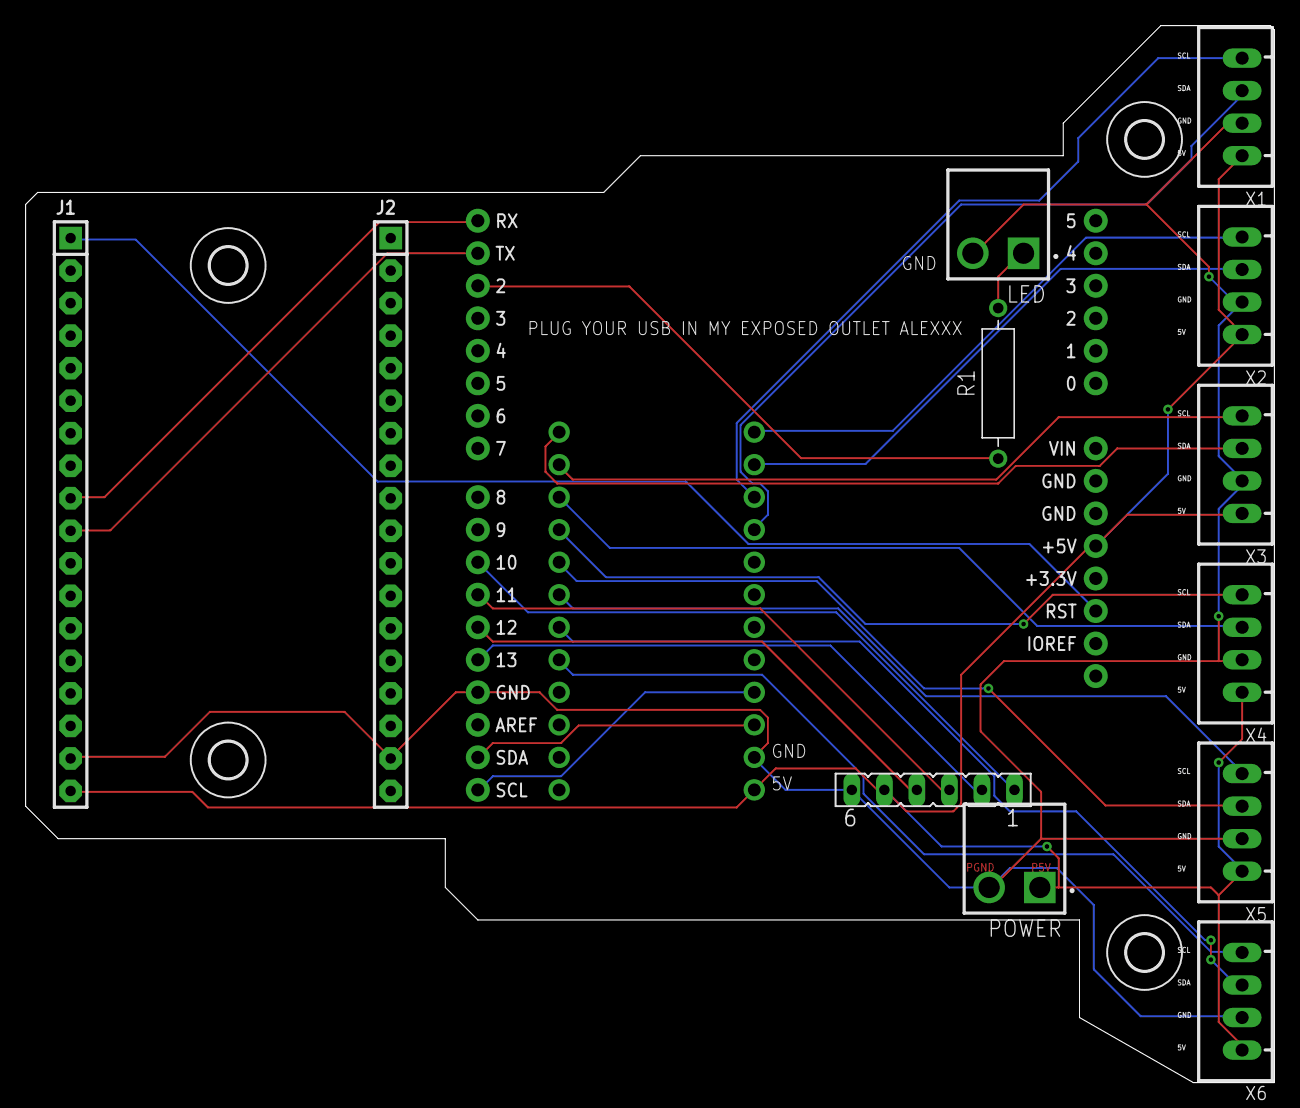
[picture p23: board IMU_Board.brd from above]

Board: 2 copper layers, 97.5 x 82.5 mm, 19 parts (0 on the bottom side), 25 nets.

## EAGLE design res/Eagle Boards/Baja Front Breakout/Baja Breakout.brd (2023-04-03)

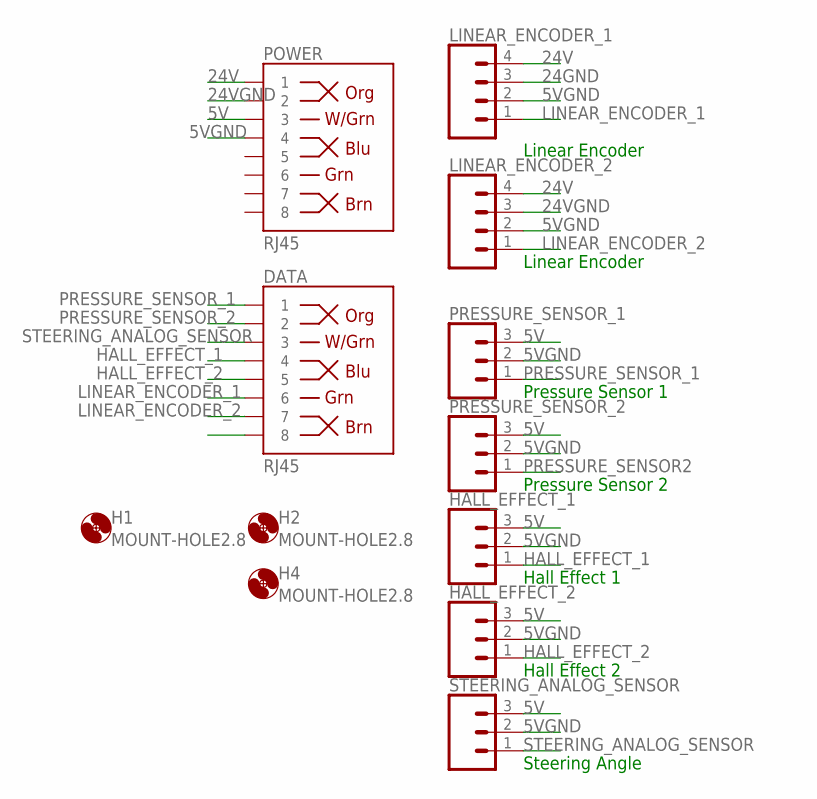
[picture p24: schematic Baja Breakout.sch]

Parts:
DATA: RJ45; RJ45-8
H1, H2, H4: MOUNT-HOLE2.8; 2,8
HALL_EFFECT_1, HALL_EFFECT_2: CONN_03; 1X03
LINEAR_ENCODER_1, LINEAR_ENCODER_2: CONN_04; 1X04
POWER: RJ45; RJ45-8
PRESSURE_SENSOR_1, PRESSURE_SENSOR_2: CONN_03; 1X03
STEERING_ANALOG_SENSOR: CONN_03; 1X03

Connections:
5V: HALL_EFFECT_1.3, HALL_EFFECT_2.3, POWER.3, PRESSURE_SENSOR_1.3, PRESSURE_SENSOR_2.3, STEERING_ANALOG_SENSOR.3
5VGND: HALL_EFFECT_1.2, HALL_EFFECT_2.2, LINEAR_ENCODER_1.2, LINEAR_ENCODER_2.2, POWER.4, PRESSURE_SENSOR_1.2, PRESSURE_SENSOR_2.2, STEERING_ANALOG_SENSOR.2
24GND: LINEAR_ENCODER_1.3
24V: LINEAR_ENCODER_1.4, LINEAR_ENCODER_2.4, POWER.1
24VGND: LINEAR_ENCODER_2.3, POWER.2
HALL_EFFECT_1: DATA.4, HALL_EFFECT_1.1
HALL_EFFECT_2: DATA.5, HALL_EFFECT_2.1
LINEAR_ENCODER_1: DATA.6, LINEAR_ENCODER_1.1
LINEAR_ENCODER_2: DATA.7, LINEAR_ENCODER_2.1
PRESSURE_SENSOR2: PRESSURE_SENSOR_2.1
PRESSURE_SENSOR_1: DATA.1, PRESSURE_SENSOR_1.1
PRESSURE_SENSOR_2: DATA.2
STEERING_ANALOG_SENSOR: DATA.3, STEERING_ANALOG_SENSOR.1

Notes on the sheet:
Linear Encoder
Pressure Sensor 2
Hall Effect 1
Hall Effect 2
Steering Angle
Pressure Sensor 1

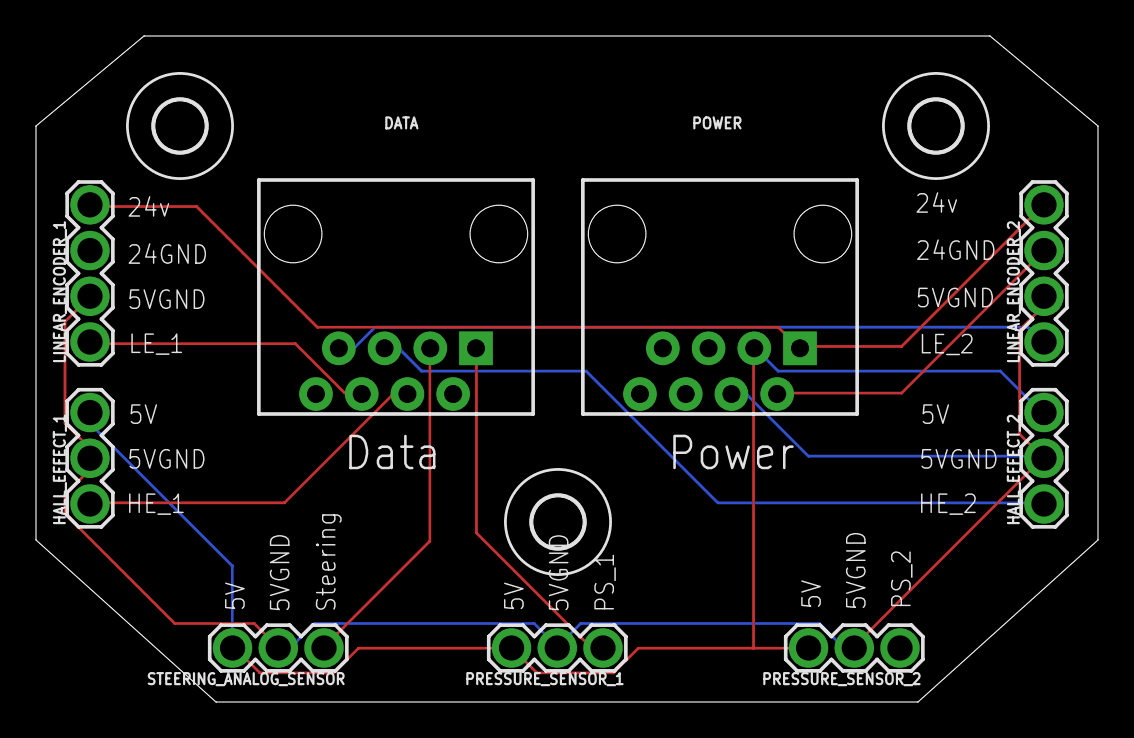
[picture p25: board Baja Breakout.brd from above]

Board: 2 copper layers, 59.0 x 37.0 mm, 12 parts (0 on the bottom side), 10 nets.

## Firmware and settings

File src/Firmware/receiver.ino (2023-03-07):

/* Heltec Automation Ping Pong communication test example
 *
 * Function:
 * 1. Ping Pong communication in two CubeCell device.
 * 
 * Description:
 * 1. Only hardware layer communicate, no LoRaWAN protocol support;
 * 2. Download the same code into two CubeCell devices, then they will begin Ping Pong test each other;
 * 3. This example is for CubeCell hardware basic test.
 *
 * HelTec AutoMation, Chengdu, China
 * 成都惠利特自动化科技有限公司
 * www.heltec.org
 *
 * this project also realess in GitHub:
 * https://github.com/HelTecAutomation/ASR650x-Arduino
 * */

#include "LoRaWan_APP.h"
#include "Arduino.h"

/*
 * set LoraWan_RGB to 1,the RGB active in loraWan
 * RGB red means sending;
 * RGB green means received done;
 */
#ifndef LoraWan_RGB
#define LoraWan_RGB 0
#endif

#define RF_FREQUENCY                                868000000 // Hz

#define TX_OUTPUT_POWER                             20        // dBm

#define LORA_BANDWIDTH                              0         // [0: 125 kHz,
                                                              //  1: 250 kHz,
                                                              //  2: 500 kHz,
                                                              //  3: Reserved]
#define LORA_SPREADING_FACTOR                       7         // [SF7..SF12]
#define LORA_CODINGRATE                             1         // [1: 4/5,
                                                              //  2: 4/6,
                                                              //  3: 4/7,
                                                              //  4: 4/8]
#define LORA_PREAMBLE_LENGTH                        8         // Same for Tx and Rx
#define LORA_SYMBOL_TIMEOUT                         0         // Symbols
#define LORA_FIX_LENGTH_PAYLOAD_ON                  false
#define LORA_IQ_INVERSION_ON                        false


#define RX_TIMEOUT_VALUE                            10000
#define BUFFER_SIZE                                 200 // Define the payload size here

char txpacket[BUFFER_SIZE];
char rxpacket[BUFFER_SIZE];

static RadioEvents_t RadioEvents;
void OnTxDone( void );
void OnTxTimeout( void );
void OnRxDone( uint8_t *payload, uint16_t size, int16_t rssi, int8_t snr );

typedef enum
{
    LOWPOWER,
    RX,
    TX
}States_t;

int16_t txNumber;
States_t state;
bool sleepMode = false;
int16_t Rssi,rxSize;


void setup() {
    Serial.begin(115200);

    txNumber=0;
    Rssi=0;

    RadioEvents.TxDone = OnTxDone;
    RadioEvents.TxTimeout = OnTxTimeout;
    RadioEvents.RxDone = OnRxDone;

    Radio.Init( &RadioEvents );
    Radio.SetChannel( RF_FREQUENCY );
    Radio.SetTxConfig( MODEM_LORA, TX_OUTPUT_POWER, 0, LORA_BANDWIDTH,
                                   LORA_SPREADING_FACTOR, LORA_CODINGRATE,
                                   LORA_PREAMBLE_LENGTH, LORA_FIX_LENGTH_PAYLOAD_ON,
                                   true, 0, 0, LORA_IQ_INVERSION_ON, 3000 );

    Radio.SetRxConfig( MODEM_LORA, LORA_BANDWIDTH, LORA_SPREADING_FACTOR,
                                   LORA_CODINGRATE, 0, LORA_PREAMBLE_LENGTH,
                                   LORA_SYMBOL_TIMEOUT, LORA_FIX_LENGTH_PAYLOAD_ON,
                                   0, true, 0, 0, LORA_IQ_INVERSION_ON, true );
    state=RX;
}



void loop()
{
  switch(state)
  {
    case TX:
      delay(1);
      sprintf(txpacket,"GOOD");
      
      turnOnRGB(COLOR_SEND,0);

      //Serial.printf("\r\nsending packet \"%s\" , length %d\r\n",txpacket, strlen(txpacket));

      Radio.Send( (uint8_t *)txpacket, strlen(txpacket) );
      state=LOWPOWER;
      break;
    case RX:
      //Serial.println("into RX mode");
        Radio.Rx( 0 );
        state=LOWPOWER;
        break;
    case LOWPOWER:
      lowPowerHandler();
        break;
        default:
            break;
  }
    Radio.IrqProcess( );
}

void OnTxDone( void )
{
  //Serial.print("TX done......");
  turnOnRGB(0,0);
  state=RX;
}

void OnTxTimeout( void )
{
    Radio.Sleep( );
    //Serial.print("TX Timeout......");
    state=TX;
}
void OnRxDone( uint8_t *payload, uint16_t size, int16_t rssi, int8_t snr )
{
    Rssi=rssi;
    rxSize=size;
    memcpy(rxpacket, payload, size );
    rxpacket[size]='\0';
    turnOnRGB(COLOR_RECEIVED,0);
    Radio.Sleep( );

    Serial.printf("%s",rxpacket);

    state=TX;
}

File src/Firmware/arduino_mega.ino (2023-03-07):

#include <TinyGPS++.h>

#define MAX_PACKETS_TO_BE_CACHED 1

#define BUSY_PIN 4

#define DIAGNOSTICS 1

#define READ_SUSPENSION 1
#define READ_GPS 0
#define READ_RPM 0

const int analogInPin[4] = {A4, A5, A6, A7};  // Analog input pin that the potentiometer is attached to

TinyGPSPlus gps_;

unsigned long timer = 0;


const byte FrameStart=0xfa;
const byte FrameEnd=0xfb;
const byte FrameESC=0xfc;

struct datapacket_struct  {
  uint16_t front_right;
  uint16_t front_left;
  uint16_t back_right;
  uint16_t back_left;
};

typedef enum
{   
    SEND_DATA,
    WAIT_TO_SEND,
    COLLECT_DATA
}States_t;

datapacket_struct dps[MAX_PACKETS_TO_BE_CACHED];

States_t state;

int num_of_datapackets = 0;

void get_new_datapacket();

void suspension(struct datapacket_struct *);

void gps(struct datapacket_struct *);

void send_datapacket();

void sendoverserial();

void print_datapackets();

void setup() {
  ADCSRA &= ~(bit (ADPS0) | bit (ADPS1) | bit (ADPS2)); // clear prescaler bits
  
  // uncomment as required
  
//  ADCSRA |= bit (ADPS0);                               //   2  
//  ADCSRA |= bit (ADPS1);                               //   4  
//  ADCSRA |= bit (ADPS0) | bit (ADPS1);                 //   8  
//  ADCSRA |= bit (ADPS2);                               //  16 
//  ADCSRA |= bit (ADPS0) | bit (ADPS2);                 //  32 
//  ADCSRA |= bit (ADPS1) | bit (ADPS2);                 //  64 
  
  ADCSRA |= bit (ADPS0) | bit (ADPS1) | bit (ADPS2);   // 128
  
  Serial.begin(115200); //monitor, only for diagnostics
  
  Serial1.begin(9600); //gps
  
  Serial2.begin(57600); //data out

  pinMode(BUSY_PIN, INPUT);

  state = COLLECT_DATA;
}

void loop() {
  delay(50);
  
  switch(state) {
    case(COLLECT_DATA):
      
      get_new_datapacket();
      
      
      #ifdef DIAGNOSTICS
      Serial.print("COLLECTING");
        
      #endif

      num_of_datapackets++;
      break;
      
    case(SEND_DATA):
      #ifdef DIAGNOSTICS      
      #endif
      send_datapacket();
      num_of_datapackets = 0;
      break;
    case(WAIT_TO_SEND):
      while(digitalRead(BUSY_PIN)) {
        #ifdef DIAGNOSTICS
        Serial.println("WAITING TO SEND");
        delay(1000);
        #endif
        }
      break;
    
   }

  if (!digitalRead(BUSY_PIN) && num_of_datapackets != 0) {
    
    state = SEND_DATA;
    
    }
  else{
    if (num_of_datapackets == MAX_PACKETS_TO_BE_CACHED) {
      state = WAIT_TO_SEND;
      num_of_datapackets = 0;
    }
    else state = COLLECT_DATA;
    }

  
}

void get_new_datapacket() {
  unsigned long init = micros();
  datapacket_struct dp;

  suspension(&dp);

  //gps(&dp);

  dps[num_of_datapackets] = dp;

  #ifdef DIAGNOSTICS  
  unsigned long diff = micros() - init;
  char charVal[100];
  sprintf(charVal, "TIME FOR DATAPACKET IS: %lu", diff);
  Serial.println(charVal);
  #endif
  }


void suspension(struct datapacket_struct *datapacket) {

  for (int i = 0; i < 4; i++) {

    int t = analogRead(analogInPin[i]);    
    
    switch(i) {
      case(0):  
        datapacket->front_right = t;
        break;
      case(1):  
        datapacket->front_left = t;
        break;
      case(2):  
        datapacket->back_right = t;
        break;
      case(3):
        datapacket->back_left = t;
        break;
      }
  }  
    
}

void gps(struct datapacket_struct *datapacket) {
  while (Serial1.available() > 0){
    gps_.encode(Serial1.read());
    if (gps_.location.isUpdated()){
      // Latitude in degrees (double)
      Serial.print("Latitude= "); 
      Serial.print(gps_.location.lat(), 6);      
      // Longitude in degrees (double)
      Serial.print(" Longitude= "); 
      Serial.println(gps_.location.lng(), 6);
    }
  }
}

#ifdef DIAGNOSTICS
void print_datapackets() {
  char temp[500];

  sprintf(temp+strlen(temp), "\n\nDATAPACKET %d ", num_of_datapackets);
  sprintf(temp+strlen(temp), "SENDING:\n\tFR:%d\n\tFL:%d\n\tBR:%d\n\tBL:%d",dps[num_of_datapackets].front_right,dps[num_of_datapackets].front_left, dps[num_of_datapackets].back_right, dps[num_of_datapackets].back_left);
  
  sprintf(temp+strlen(temp), "\nTIMER IN MS: %lu", timer);  

  Serial.println(temp);
}
#endif

void send_datapacket() {
  //for (int i = 0; i < sizeof(buffer_message); i++) Serial.write(buffer_message[i]);
  int size_of_packet = 0;
  Serial.print("\npacket sent: ");
  Serial.print(dps[0].front_right); Serial.print(","); Serial.print(dps[0].front_left); Serial.print(","); Serial.print(dps[0].back_right); Serial.print(","); Serial.print(dps[0].back_left);
  Serial.print("\n");  
  
   Serial2.write(FrameStart);
  for (int s = 0; s < num_of_datapackets; s++) {
    
    byte* structPtr = (byte*) &dps[s];
    
    for (size_t i=0; i < sizeof(dps[s]); i++) {
      if ((structPtr[i] == FrameStart) || (structPtr[i] == FrameEnd) || (structPtr[i] == FrameESC)) {
        Serial.println("special byte spent");

        Serial2.write(FrameESC);
        Serial2.write(structPtr[i] ^ 0xA5);
      } else Serial2.write(structPtr[i]);
      
      size_of_packet++;
    }
  }

  Serial2.write(FrameEnd);

  Serial.print("SENT ");
  Serial.print(size_of_packet);
  Serial.print("BYTES");
  Serial.println();  
}

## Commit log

2022-07-13 fixing return issue (#11)
    * test code review
    * test #2
    * Add files via upload
    * Delete LoRa GPS Code directory
    * Add files via upload
    * very important message (#7)
    * test
    * fixing return issue
    [BAJA_BNO055.ino]
2022-08-06 Update How to install LoRa GPS in Arduino IDE.txt
2022-08-06 adding arduino ide into vs code
2022-08-06 testing uploading to LoRa GPS board
2022-08-07 adding beta I2C communication methods
2022-08-08 Implementing I2C Handling
2022-10-10 Adding Power Board Files
    [Battery_Board_Case.3mf, Battery_Board_Lid.3mf, Battery_Board_Seal.3mf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]
2023-01-15 added the imu code and the python code (#19)
    * WE GONNA GET IT GOINGGGG
    * yabagagoo
    * yessirr
    * we graping
    * asdasd
    * added arduino code
    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
2023-01-15 Addition of Arduino Code (#20)
    this code is literally beautiful
    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
2023-02-10 Updating Main Branch (#14)
    * Update README.md
    * adding LoRa GPS examples
    * adding product page
    * adding more examples
    * Update How to install LoRa GPS in Arduino IDE.txt
    * adding arduino ide into vs code
    * te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
    [Battery_Board_Case.3mf, Battery_Board_Lid.3mf, Battery_Board_Seal.3mf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]
2023-02-10 restructuring of files (#21)
    * restructuring github
    ---------
    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
2023-02-10 forgot to get upstream (#22)
    * updating some more
    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
2023-02-10 still restructuring (#26)
    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
2023-02-10 tech issues (#28)
    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
2023-02-10 maybe this works (#29)
    * fixing return issue (#11)
    this code is liter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
    [BAJA_BNO055.ino, LoraSendGPS.ino, RGB_example.ino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]
2023-02-10 moving file (#34)
    [Battery_Board_Case.3mf, Battery_Board_Lid.3mf, Battery_Board_Seal.3mf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]
2023-02-11 adding imu code (#38)
2023-02-11 Pyqt interface (#39)
    * its gonna get messy in here
    * im lost
    * getting something going
    * kinda working
    * building it out
    * chugging
    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
2023-02-11 Mega to htc boards serial com (#41)
    this is the lora reciver code AND the serial reciever, combine them
    * Update main.ino
    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
2023-02-11 Pyqt interface (#42)
    * its workingggg
    * Update current_main.py
    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
2023-02-13 reorganizing files
    [Battery_Board_Case.3mf, Battery_Board_Lid.3mf, Battery_Board_Seal.3mf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]
2023-02-25 updating gps (#52)
    * askdnasd
    * Py qt interface (#46)
    * askdnasd
    * asdj
    * I fixed Alex's stupid lists
    * i delete extra new lines
    * Dorian branch (#47)
    * askdnasd
    * i delete extra new lines
    * Hz monitor (#48)
    * askdnasd
    * i delete extra new lines
    * Added a hertz graph and class
    Alex wants my mom bad.
    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
    [rx.ino]
2023-02-25 Gps (#53)
    * poop
    * updating gps (#52)
    * lordy
    * Delete lora_transmit.py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
    [fake_gps.ino]
2023-03-12 Gps (#64)
    * updating gps (#63)
    * Delete lora_transmit.py
    * Ad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
    [temp_gps_parser.ino]
2023-03-13 Gps (#65)
    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
    [temp_gps_parser.ino]
2023-03-25 New serial parser (#68)
    * updating serial parser (#66)
    * dadad (#61)
    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
    [alldata_sinusoidal.csv]
2023-04-03 board svgs
2023-04-04 reorganized files
    [Baja Breakout.brd, Baja Breakout.sch, Battery_Board_Case.3mf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]

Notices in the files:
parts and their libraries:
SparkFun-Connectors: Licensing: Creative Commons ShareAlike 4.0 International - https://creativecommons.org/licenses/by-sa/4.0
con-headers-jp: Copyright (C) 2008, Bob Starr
